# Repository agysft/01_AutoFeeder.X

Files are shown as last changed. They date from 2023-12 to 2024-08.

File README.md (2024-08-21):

# AutoFeeder
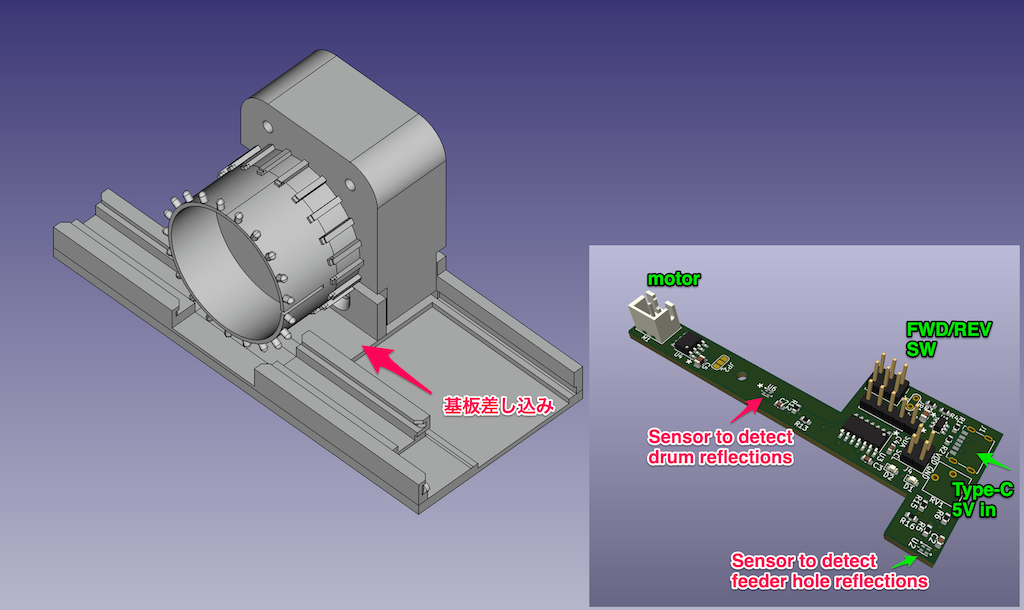
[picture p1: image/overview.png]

This is a test project for an auto-feeder for CompactPnP. When the switch is pressed, the feeder moves one frame. It includes a program and a schematic. The program was written in PIC MPLAB X IDE. The schematic is written in KiCAD and the printed circuit board is made. The structure was made with a 3D printer.

---
これはCompactPnP用のオートフィーダーのテスト用プロジェクトです。スイッチが押されるとフィーダーが一コマ移動します。プログラムと回路図を含みます。プログラムはPIC MPLAB X IDEで書きました。回路図はKiCADで書き、プリント基板を作っています。構造物は3Dプリンターで作りました。

---
### Rev.01
* [demo](image/ezgif.com-video-to-gif-converted.gif)
* [schematics](schematics/AutoFeeder_Drum-type_new/20231123_R1/AutoFeeder_Drum-type.pdf) 
* block chart
```mermaid
graph LR
  A[Timer2]-->B[PWM3]-->C
  subgraph BA6211
  C[FWD]
  E[REV]
  end
  A-->D[PWM4]-->E
  F[Sensor0]-->|-|M[CMP2]-->N[LED Green]
    L[FVR 1.024V]-->|+|M
    L-->|+|Q
  I[Sensor1]-->|-|Q[CMP1]-->K[LED Red]
```
---

### Rev.02
フォトセンサーの感度を切り替える回路と、ドラムの角度を取得するためのAS5600という磁気センサーと、I2CのLCDを接続できるようにしました。Add a circuit to switch the sensitivity of the photo sensor, a magnetic sensor named AS5600 to get the angle of the drum, and the LCD.
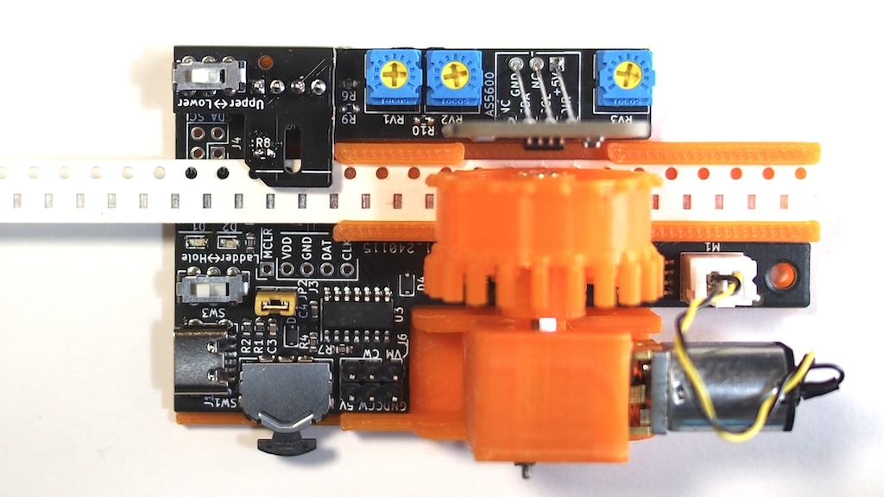
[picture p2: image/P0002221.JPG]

* [demo](image/20240212_AutoFeederTest-ezgif.com-video-to-gif-converter.gif)
* [schematics](schematics/AutoFeeder_Drum-type_new/20240107_Rev02/AutoFeeder_Drum-type.pdf) 
* block chart

```mermaid
graph LR
  G[Senror1 Radder detector]--> S
  F[Sensor0 Tape-hole detector]--> S
  S{Switch} -->| M- |M
  subgraph BA6211
  C[FWD]
  E[REV]
  end
  BA6211 --- Z[Motor]
  subgraph PIC16F1705
  A[Timer2 50KHz]-->D
  A-->B
  B[PWM3 -- RC5]---C
  D[PWM4 -- RC4]---E
  L[FVR 2.048V]-->| P+ |M[CMP2 -- RA0]
  RA4[GPIO RA4 Open Drain]
  RA5[GPIO RA5 Open Drain]
  end
  M-->N[LED]
  AS5600---|I2C|PIC16F1705
  PIC16F1705---|I2C|LCD
  
  H[Optical Sensor Sensitivity Selector]---RA4
  H---RA5
```

* High-Endurance Flash memory (HEF) usage 0x1F80-0x1F9F
  | Offset Address | note (1 word = 14-bit wide) |
  |:--:|---- 
  | 25 .. 31 | No Use |
  | 2 .. 24 | Tape hole position data (12-bit wide) |
  | 1 | Tape-Color data (White/Transparent/Black)|
  | 0 | AS5600 Magnetic data of origin (12-bit wide) |
* HEF 0x1FA0-0x1FFF is not use.

---
### AutoFeeder2 Rev.1
Autofeeder Rev.02の機能はそのままに、基板を縦置きする事で省スペース化を図りました。また、透過型のフォトインタラプターCNZ1023を使えるようにしました。The functions of the Autofeeder are retained, but the board is placed vertically to save space. Transmissive photo interrupter CNZ1023 can also be used.
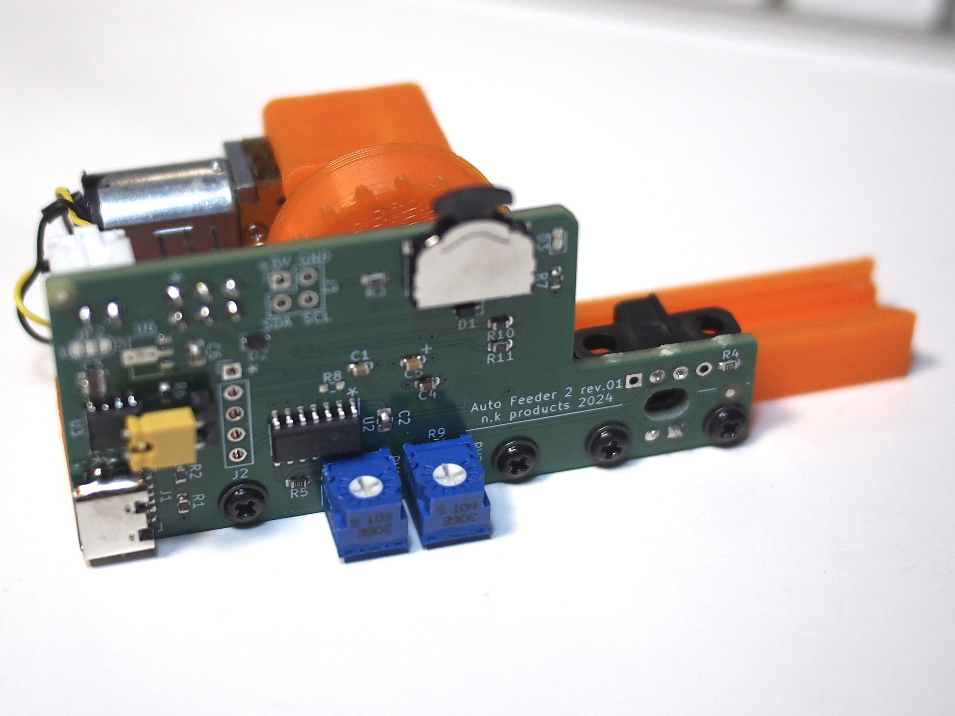
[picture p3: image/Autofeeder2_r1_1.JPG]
AF2R1_pict1


* [demo](image/20240803_AutoFeeder_Test2.gif)
* [schematics](schematics/AutoFeeder_Drum-type_2/20240519_AF2_rev1/AutoFeeder_Drum-type.pdf) 

---
### Tips

* PIC16F1705でI2C を設定する。何故か400kHzに設定するとハングします。「Registers」で SSP1ADD = 0x9 (=400KHz)に設定することは可能。
  
  Setting I2C on the PIC16F1705. It hangs when set to 400kHz. It is possible to set SSP1ADD = 0x9 (=400KHz) in "Registers".
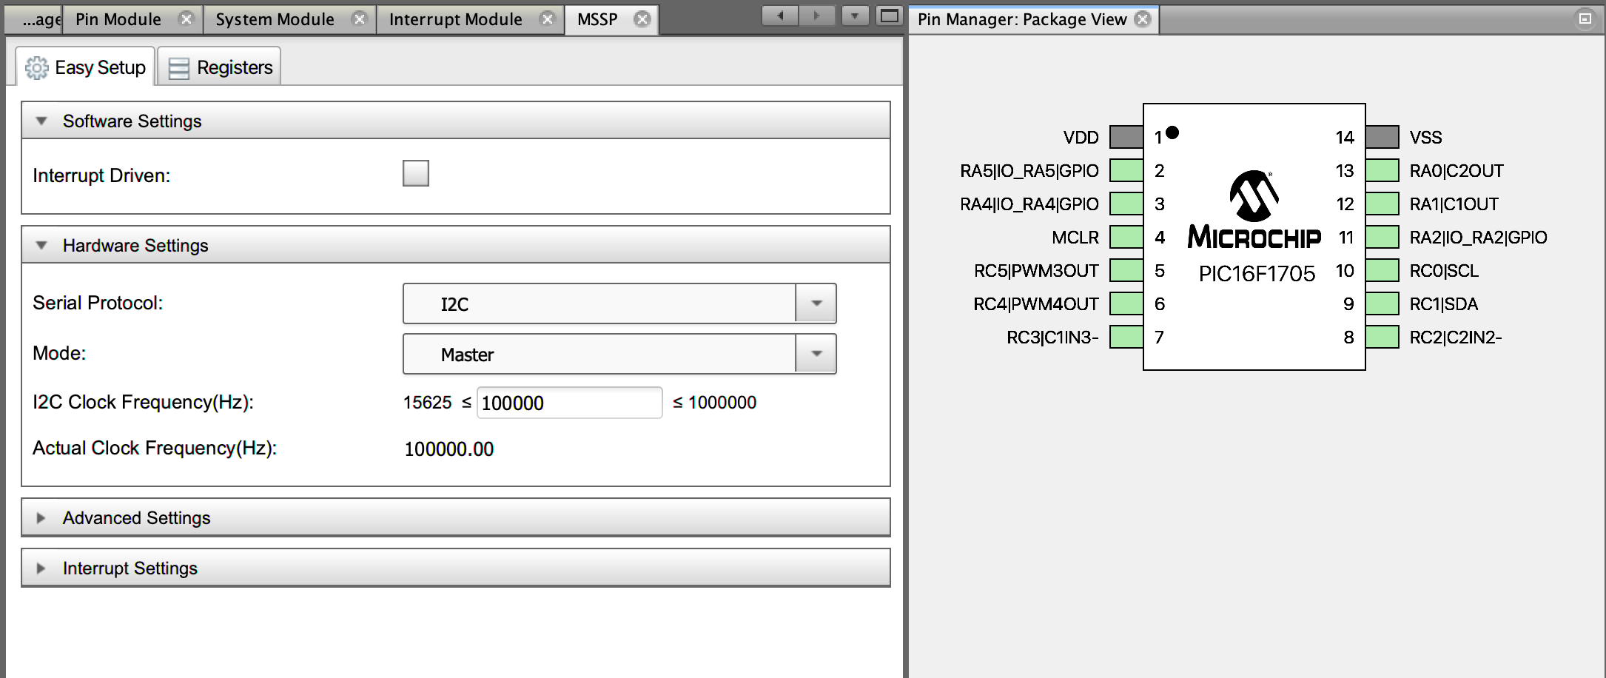
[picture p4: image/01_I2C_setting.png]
  

* このI2Cのサンプルコードがよく出来ていてそのままincludeして使える。
  This I2C sample code is well done and can be included and used as is.
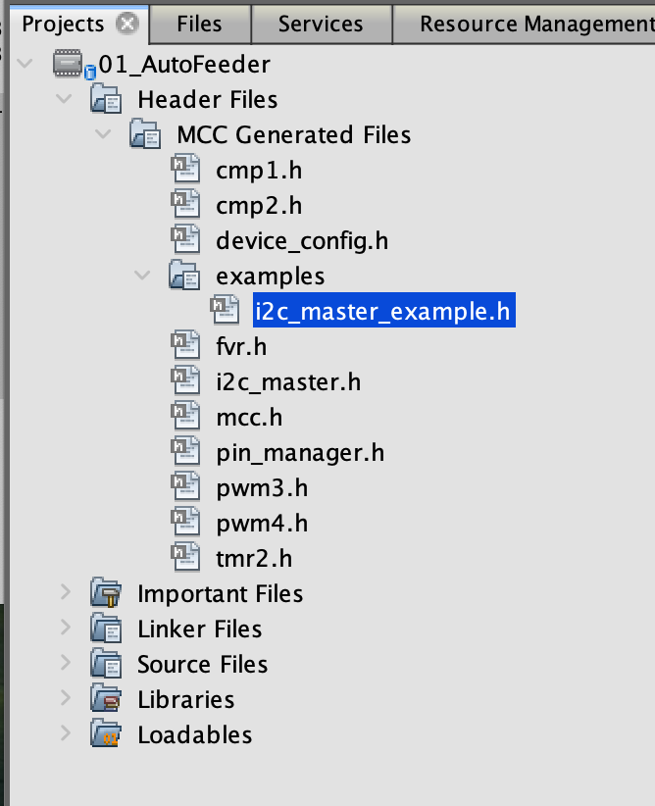
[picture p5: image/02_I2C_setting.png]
  

* HEF-block範囲にプログラムが書かれないようにする設定。
  Settings to prevent programs from being written in the HEF-block range
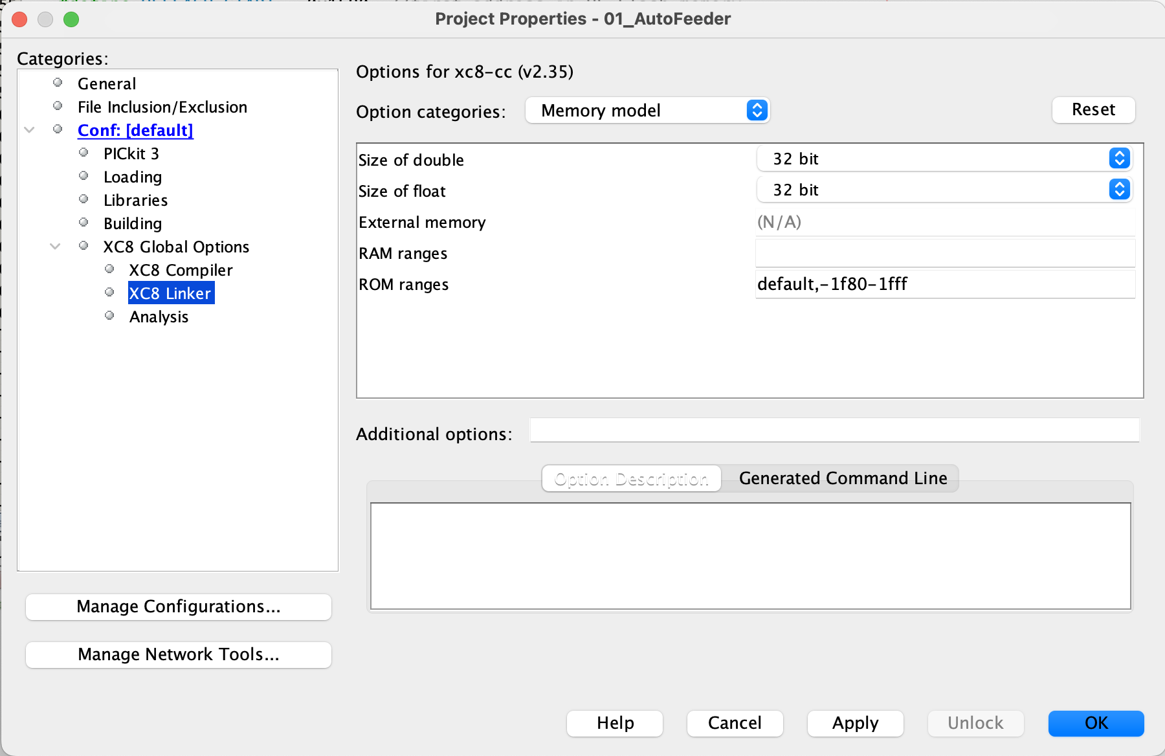
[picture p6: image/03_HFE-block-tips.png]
  

* PICに書いた時にHEFブロックが初期化されない設定。
  Settings to prevent the HEF-block from being initialized when writing to the PIC
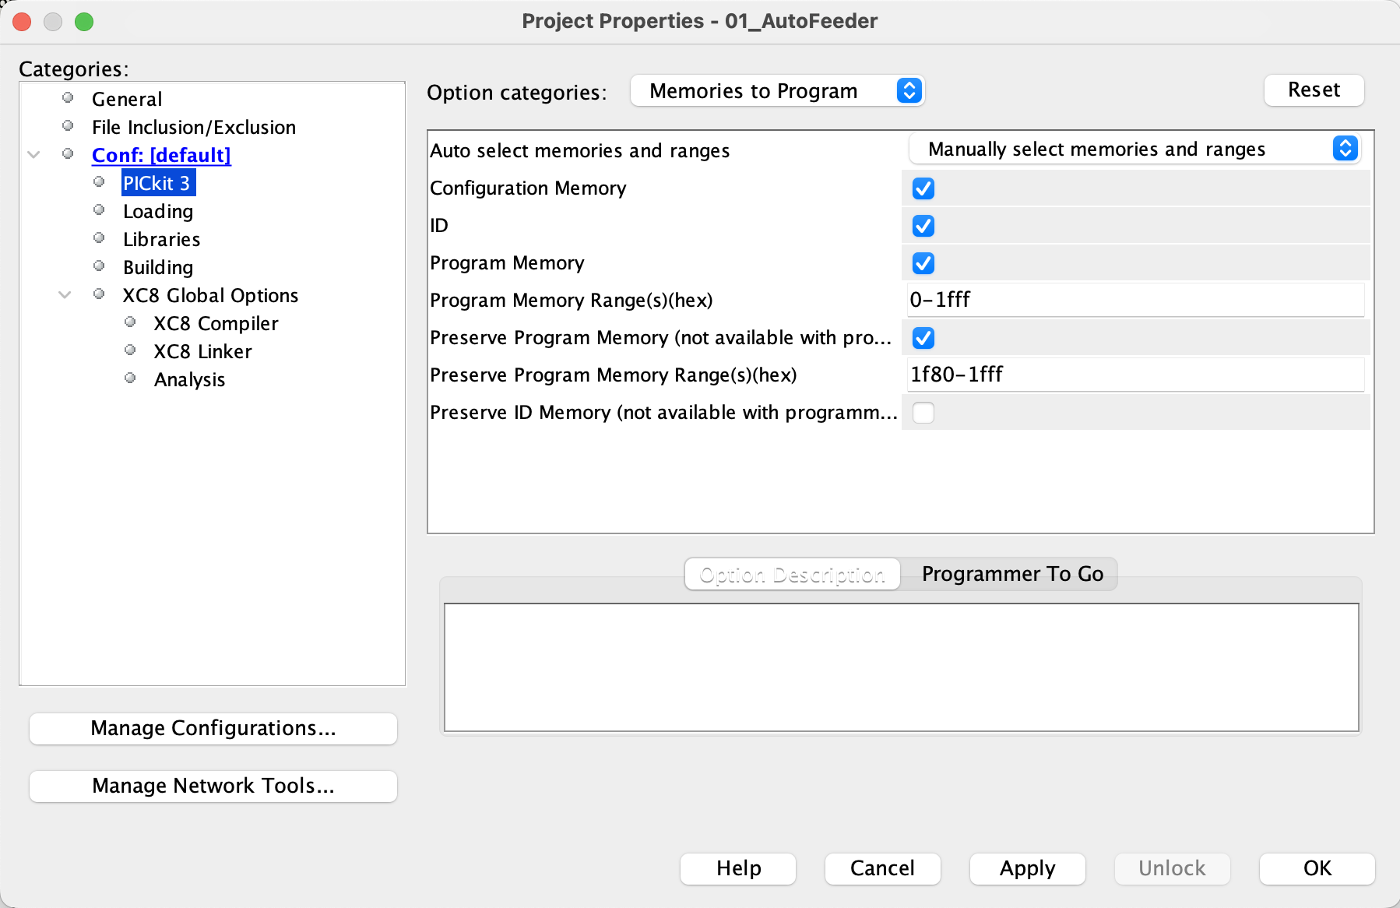
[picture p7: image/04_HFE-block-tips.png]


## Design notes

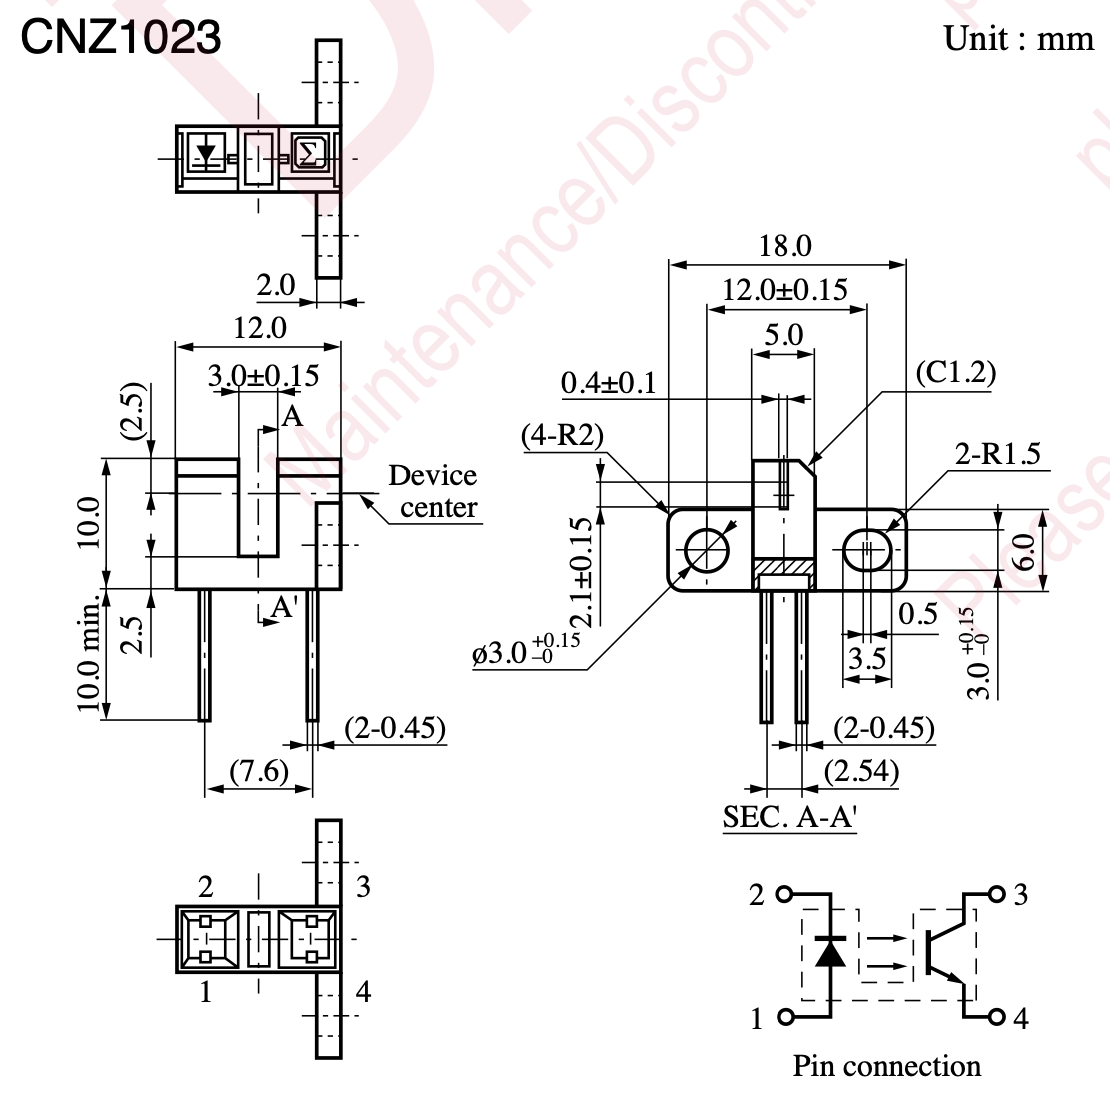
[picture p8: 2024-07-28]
schematics/AutoFeeder_Drum-type_2/CNZ1023.png

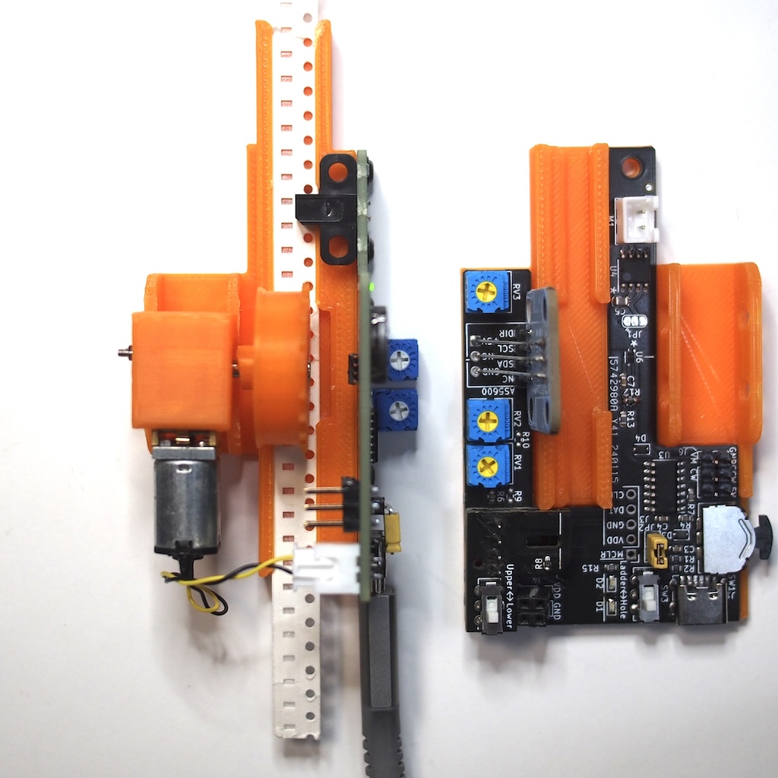
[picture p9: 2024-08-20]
image/Autofeeder2_r1_2.JPG

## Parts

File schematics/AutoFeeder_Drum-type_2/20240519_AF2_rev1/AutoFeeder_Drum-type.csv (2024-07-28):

ID | 指定子 | パッケージ | 数量 | 名称 | 供給業者、参考資料
1 | R7,R3,R4 | R_0603_1608Metric | 3 | 1k
2 | U3 | SOIC-8_3.9x4.9mm_P1.27mm | 1 | ZXBM5210-S
3 | R5 | R_0603_1608Metric | 1 | 1.5k
4 | J3 | PinHeader_2x02_P2.54mm_Vertical | 1 | Conn_02x02_Odd_Even
5 | C1 | C_0603_1608Metric | 1 | 0.01u
6 | C5 | C_0603_1608Metric | 1 | 1u
7 | JP2 | SolderJumper-3_P1.3mm_Bridged12_RoundedPad1.0x1.5mm_NumberLabels | 1 | SolderJumper_3_Bridged12
8 | J2 | PinHeader_1x05_P2.54mm_Vertical | 1 | Conn_01x05
9 | U2 | SOIC-14_3.9x8.7mm_P1.27mm | 1 | PIC16F1705-I/SO
10 | C2,C6 | C_0805_2012Metric | 2 | 0.1u
11 | R11,R2,R1,R10 | R_0603_1608Metric | 4 | 5.1k
12 | R6 | R_0603_1608Metric | 1 | 10k
13 | U6 | SOT-89-3 | 1 | L78L05_SOT89
14 | RV2,RV1 | Potentiometer_ACP_CA6-H2,5_Horizontal | 2 | 20k
15 | D3 | LED_0603_1608Metric | 1 | LED
16 | J1 | USB_C_6 | 1 | USB_C_Receptacle_6
17 | SW1 | THMU26_2 | 1 | TMHU26
18 | R9 | R_0603_1608Metric | 1 | 20k
19 | R8 | R_0603_1608Metric | 1 | 9.1k
20 | D2,D1 | D_SOD-323F | 2 | 1SS355VM
21 | C4 | C_0603_1608Metric | 1 | 0.1u
22 | J7 | PinHeader_1x04_P2.54mm_Vertical | 1 | Conn_01x04
23 | U5 | NJL5901AR-1 | 1 | NJL5901AR-1
24 | C3 | C_0805_2012Metric | 1 | 10u
25 | JP3 | SolderJumper-3_P1.3mm_Bridged12_RoundedPad1.0x1.5mm | 1 | SolderJumper_3_Bridged12
26 | M1 | JST_XH_B2B-XH-A_1x02_P2.50mm_Vertical | 1 | Motor_DC
27 | JP1 | PinHeader_1x02_P2.54mm_Horizontal | 1 | Jumper_2_Bridged
28 | J6,J5 | PinHeader_1x01_P2.54mm_Vertical | 2 | Conn_01x01
29 | U4 | SOP-8_3.9x4.9mm_P1.27mm | 1 | AS5600
30 | U1 | CNZ1023 | 1 | CNZ1023
31 | J4 | PinHeader_2x03_P2.54mm_Vertical | 1 | Conn_02x03_Odd_Even

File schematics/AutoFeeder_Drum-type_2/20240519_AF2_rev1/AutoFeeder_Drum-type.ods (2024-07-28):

ID | 指定子 | パッケージ | 数量 | 名称 | 供給業者、参考資料 |  | 販売コード |  |  | 購入数 | 価格合計
5 | C1 | C_0603_1608Metric | 1 | 0.01u |  |  |  |  |  |  | 0
10 | C2,C6 | C_0805_2012Metric | 2 | 0.1u |  |  |  |  |  |  | 0
24 | C3 | C_0805_2012Metric | 1 | 10u |  |  |  |  |  |  | 0
21 | C4 | C_0603_1608Metric | 1 | 0.1u |  |  | 116143 | 110 |  | 1 | 110 | x40個入り
6 | C5 | C_0603_1608Metric | 1 | 1u |  |  | 114526 | 100 |  | 1 | 100 | x20個入り
20 | D2,D1 | D_SOD-323F | 2 | 1SS355VM |  |  |  |  |  |  | 0
15 | D3 | LED_0603_1608Metric | 1 | LED 黄色 |  | * | 111880 | 100 | 100 | 1 | 100 | x10個入り
 |  |  | 1 | LED 白色 |  |  | 111882 | 200 | 200 | 2 | 400 | x20個入り
16 | J1 | USB_C_6 | 1 | USB_C_Receptacle_6 |  |  |  |  |  |  | 0
8 | J2 | PinHeader_1x05_P2.54mm_Vertical | 1 | Conn_01x05 |  |  |  |  |  |  | 0
4 | J3 | PinHeader_2x02_P2.54mm_Vertical | 1 | Conn_02x02_Odd_Even |  |  |  |  |  |  | 0
31 | J4 | PinHeader_2x03_P2.54mm_Vertical | 1 | Conn_02x03_Odd_Even |  |  |  |  |  |  | 0
28 | J6,J5 | PinHeader_1x01_P2.54mm_Vertical | 2 | Conn_01x01 |  |  |  |  |  |  | 0
22 | J7 | PinHeader_1x04_P2.54mm_Vertical | 1 | Conn_01x04 |  |  |  |  |  |  | 0
27 | JP1 | PinHeader_1x02_P2.54mm_Horizontal | 1 | Jumper_2_Bridged |  |  |  |  |  |  | 0
7 | JP2 | SolderJumper-3_P1.3mm_Bridged12_RoundedPad1.0x1.5mm_NumberLabels | 1 | SolderJumper_3_Bridged12 |  |  |  |  |  |  | 0
25 | JP3 | SolderJumper-3_P1.3mm_Bridged12_RoundedPad1.0x1.5mm | 1 | SolderJumper_3_Bridged12 |  |  |  |  |  |  | 0
26 | M1 | JST_XH_B2B-XH-A_1x02_P2.50mm_Vertical | 1 | Motor_DC |  |  |  |  |  |  | 0
11 | R11,R2,R1,R10 | R_0603_1608Metric | 4 | 5.1k |  |  |  |  |  |  | 0
3 | R5 | R_0603_1608Metric | 1 | 1.5k |  |  |  |  |  |  | 0
12 | R6 | R_0603_1608Metric | 1 | 10k |  |  |  |  |  |  | 0
1 | R7,R3,R4 | R_0603_1608Metric | 3 | 1k |  |  |  |  |  |  | 0
19 | R8 | R_0603_1608Metric | 1 | 9.1k |  |  |  |  |  |  | 0
18 | R9 | R_0603_1608Metric | 1 | 20k |  |  |  |  |  |  | 0
14 | RV2,RV1 | Potentiometer_ACP_CA6-H2,5_Horizontal | 2 | 20k →100k |  | * | 113740 | 40 | 80 | 4 | 160
 |  |  | 2 | 10k |  |  | 113739 | 40 | 80 | 4 | 160
 |  |  | 2 | 半固定ボリューム GF063P 50kΩ |  |  | 114908 | 30 | 60 | 4 | 120
17 | SW1 | THMU26_2 | 1 | TMHU26 |  |  |  |  |  |  | 0
30 | U1 | CNZ1023 | 1 | CNZ1023 |  | * | 109668 | 20 | 20 | 4 | 80
9 | U2 | SOIC-14_3.9x8.7mm_P1.27mm | 1 | PIC16F1705-I/SO |  |  | 113571 | 170 | 170 | 4 | 680
2 | U3 | SOIC-8_3.9x4.9mm_P1.27mm | 1 | ZXBM5210-S BD6231(36V耐圧) |  |  | 105088 | 200 | 200 | 2 | 400
29 | U4 | SOP-8_3.9x4.9mm_P1.27mm | 1 | AS5600 |  |  |  |  |  |  | 0
23 | U5 | NJL5901AR-1 | 1 | NJL5901AR-1 |  |  |  |  |  |  | 0
13 | U6 | SOT-89-3 | 1 | L78L05_SOT89 NJM78L05SU3 |  | * | 111320 | 30 | 30 | 4 | 120
 |  |  | 1 | BatteryHolder_Keystone_2466_1xAAA |  |  | 102670 | 40 | 40 | 4 | 160
 |  |  | 1 | トロイダルコア FT-37-75 |  |  | 116922 | 150 | 150 | 4 | 600
 |  |  | 1 | 2種ポリウレタン銅線 2UEW 0.4mm 10m |  |  | 113709 | 220 | 220 | 1 | 220
 |  |  |  |  |  |  |  |  |  |  | 0
 |  |  |  |  |  |  |  |  |  |  | 0
 |  |  |  |  |  |  |  |  |  |  | 0
 |  |  |  |  |  |  |  |  |  |  | 0
 |  |  |  |  |  |  |  |  | 1350 |  | 3410

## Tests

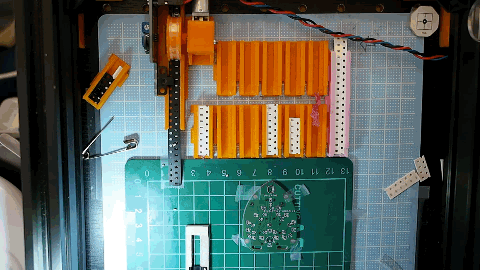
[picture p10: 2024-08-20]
image/20240803_AutoFeeder_Test2.gif

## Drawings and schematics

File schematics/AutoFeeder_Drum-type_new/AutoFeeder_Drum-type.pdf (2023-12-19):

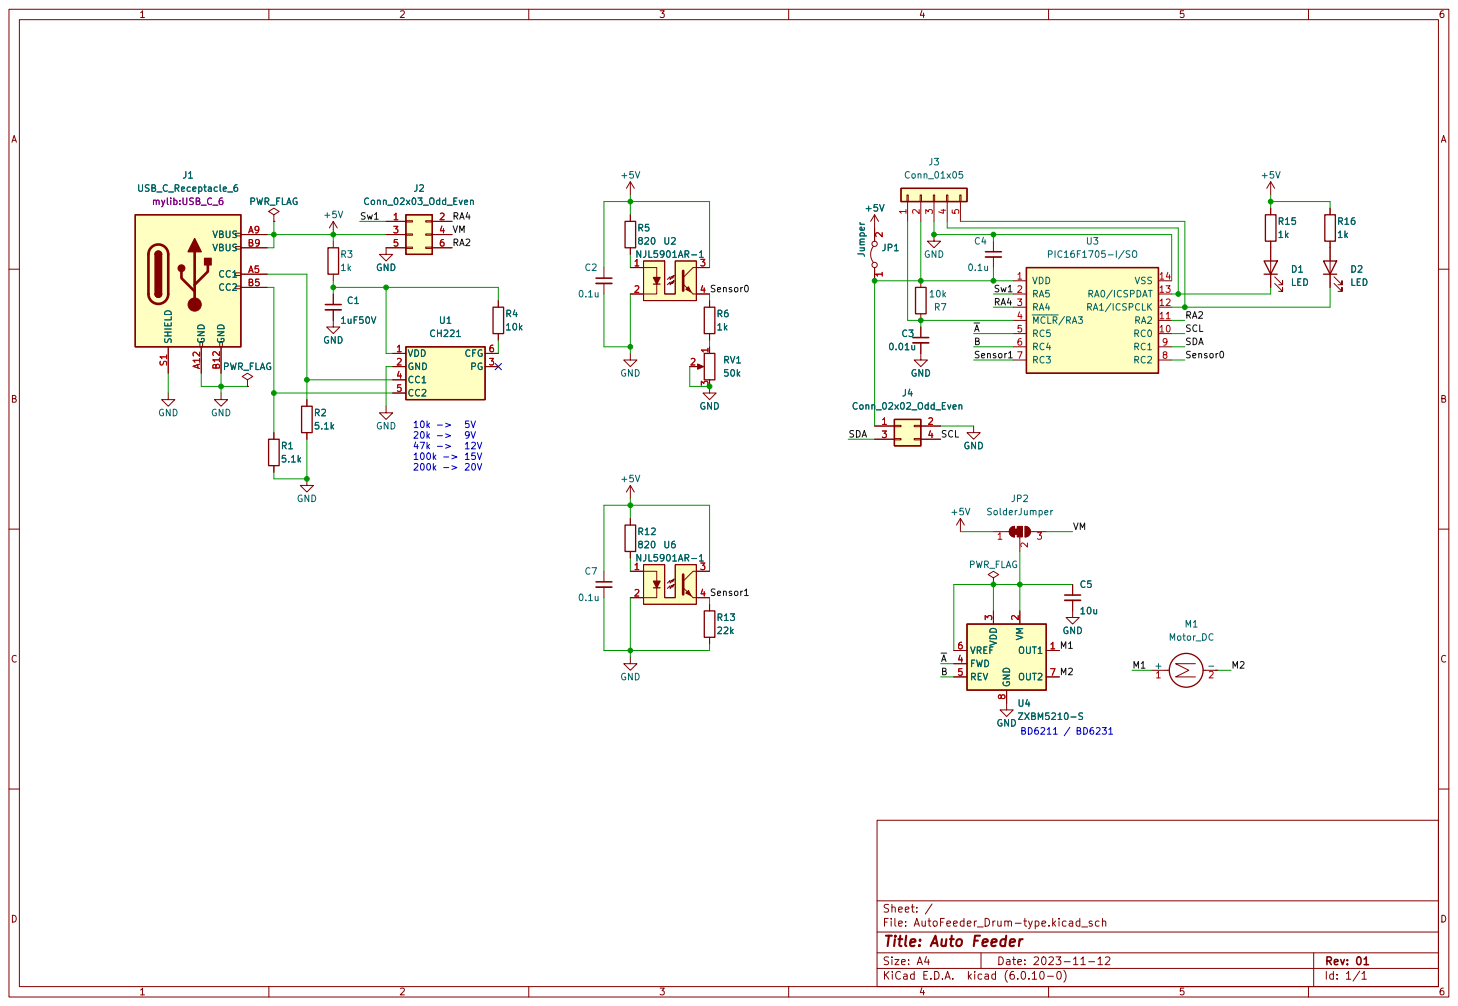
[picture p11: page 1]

1 2 JP1 Jumper GND GND OUT1 1 VM

3 FWD 4 REV 5 VREF 6 OUT2 7 GND

File: AutoFeeder_Drum-type.kicad_sch Sheet: /
Id: 1/1 Title: Auto Feeder

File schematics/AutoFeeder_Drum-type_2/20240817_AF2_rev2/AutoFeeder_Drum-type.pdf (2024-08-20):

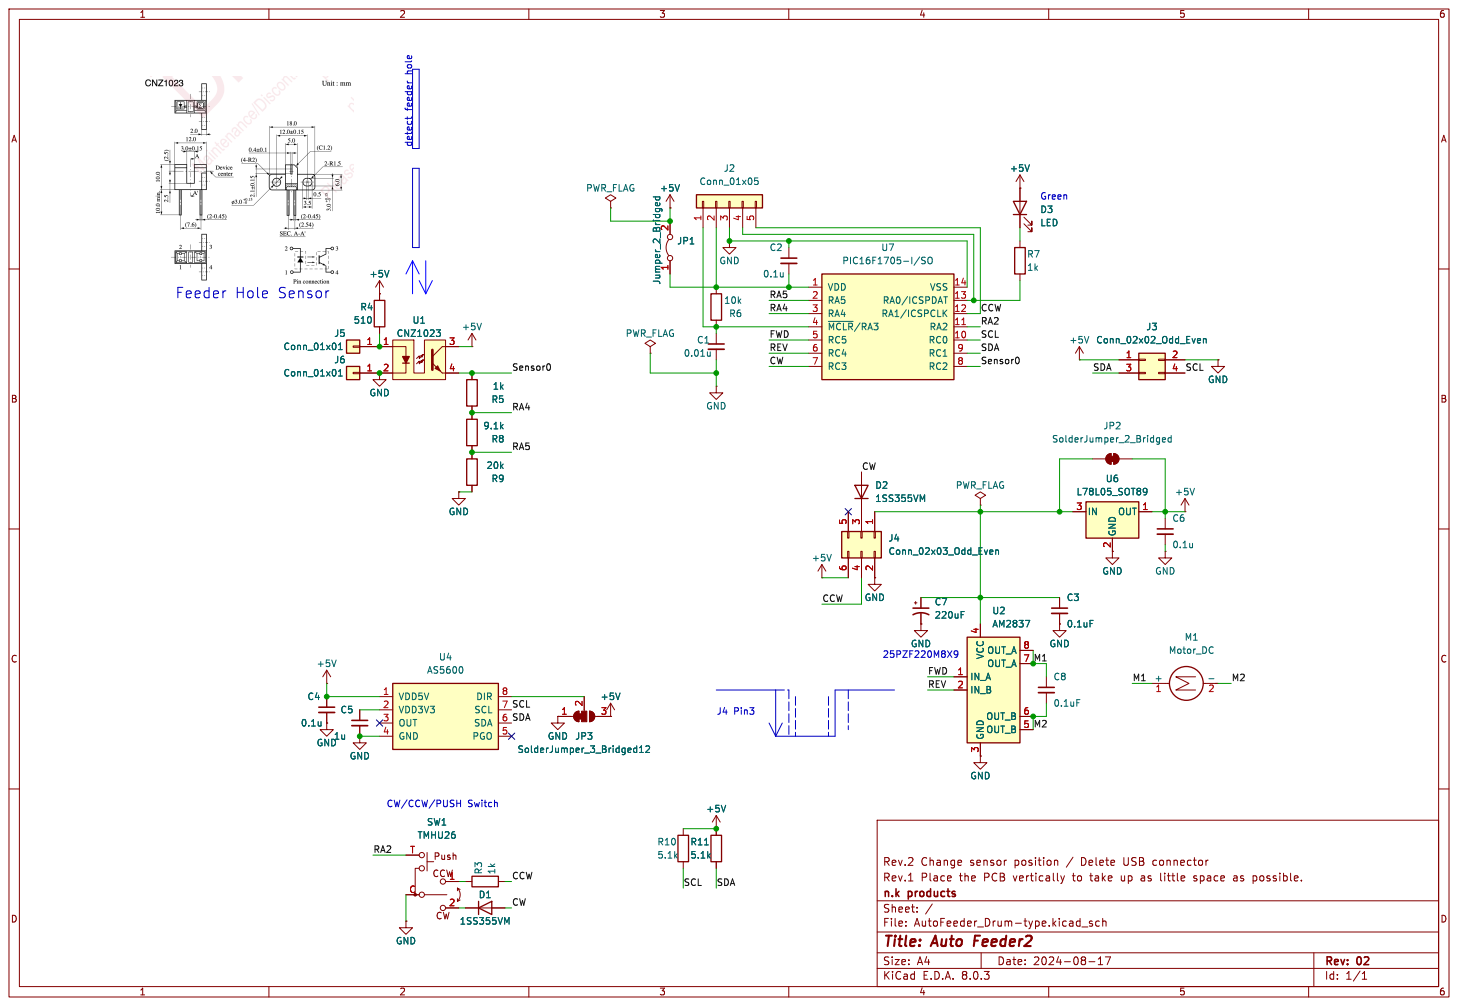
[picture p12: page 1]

Green detect feeder hole

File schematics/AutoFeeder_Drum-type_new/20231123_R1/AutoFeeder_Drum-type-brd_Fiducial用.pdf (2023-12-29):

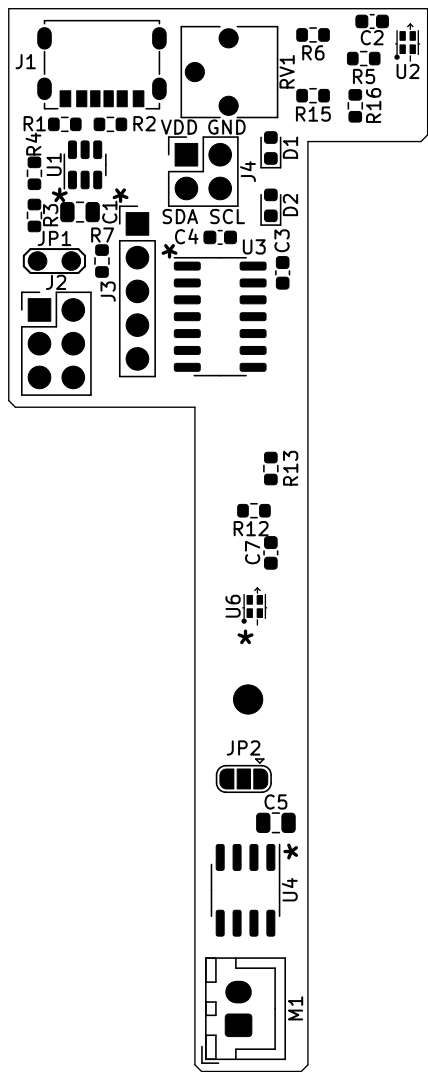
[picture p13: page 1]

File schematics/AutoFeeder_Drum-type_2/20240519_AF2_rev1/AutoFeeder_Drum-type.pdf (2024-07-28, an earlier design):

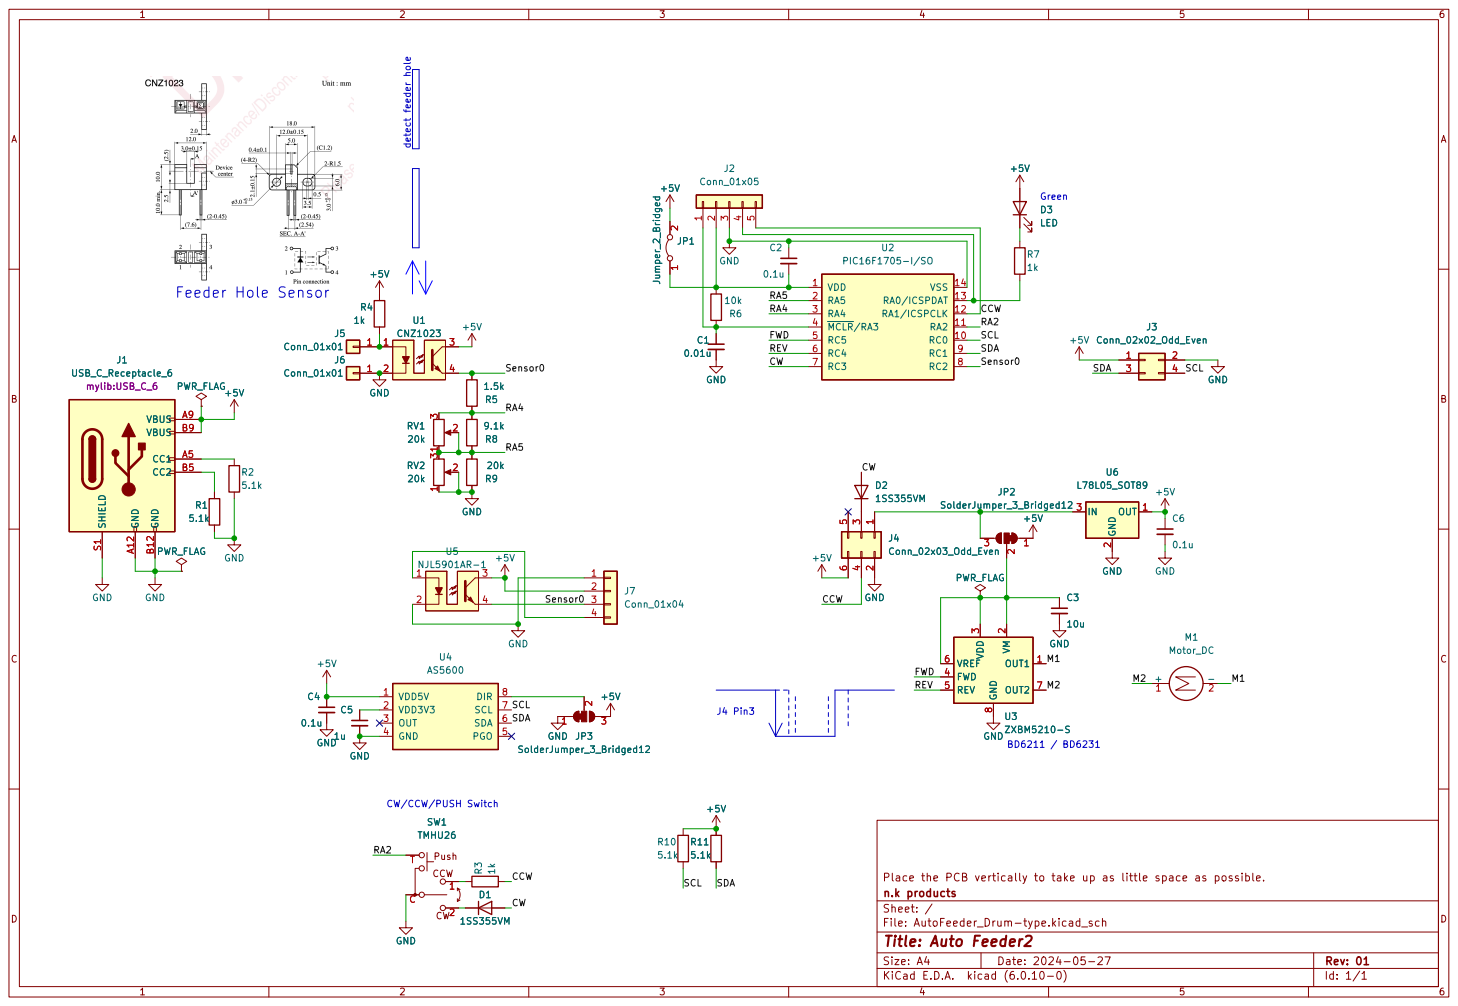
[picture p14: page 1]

J4 Pin3 CW/CCW/PUSH Switch Feeder Hole Sensor

3 FWD 4 REV 5 VREF 6 OUT2 7 GND

Place the PCB vertically to take up as little space as possible.
File: AutoFeeder_Drum-type.kicad_sch Sheet: / n.k products

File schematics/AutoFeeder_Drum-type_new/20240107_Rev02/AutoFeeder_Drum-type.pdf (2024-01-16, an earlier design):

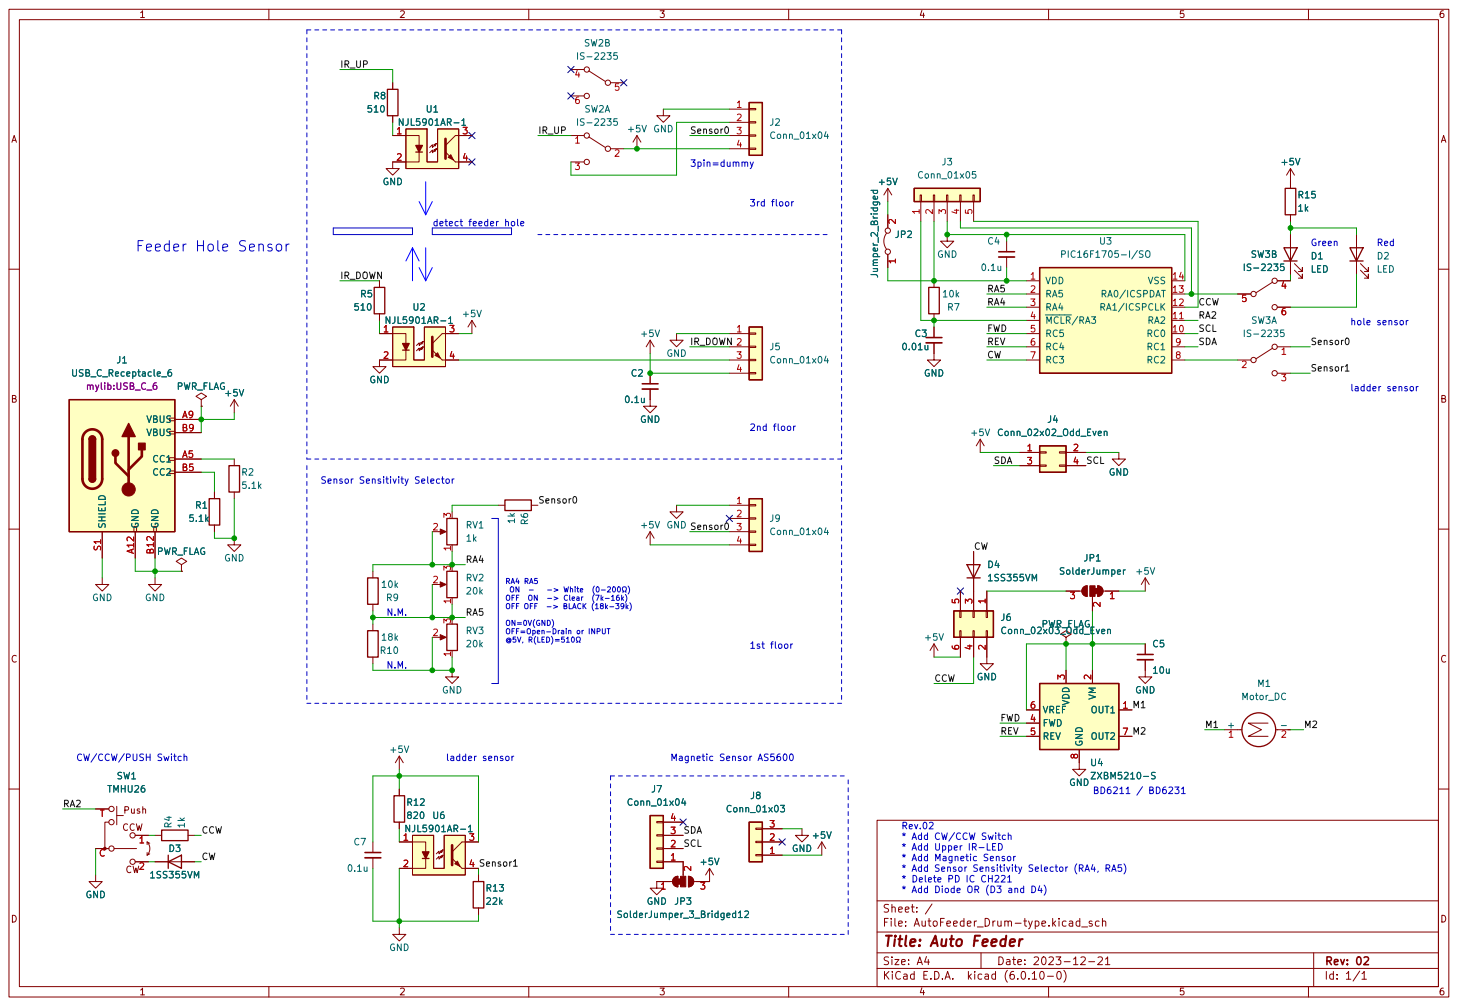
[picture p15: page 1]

þÿ ON  -   -> White  (0-200©) OFF ON -> Clear (7k-16k) OFF OFF -> BLACK (18k-39k) ON=0V(GND) OFF=Open-Drain or INPUT

* Add Diode OR (D3 and D4) 1st floor Magnetic Sensor AS5600

3 FWD 4 REV 5 VREF 6 OUT2 7 GND

* Add CW/CCW Switch
* Add Upper IR-LED
* Add Magnetic Sensor
* Add Sensor Sensitivity Selector (RA4, RA5) * Delete PD IC CH221

Id: 1/1 Title: Auto Feeder

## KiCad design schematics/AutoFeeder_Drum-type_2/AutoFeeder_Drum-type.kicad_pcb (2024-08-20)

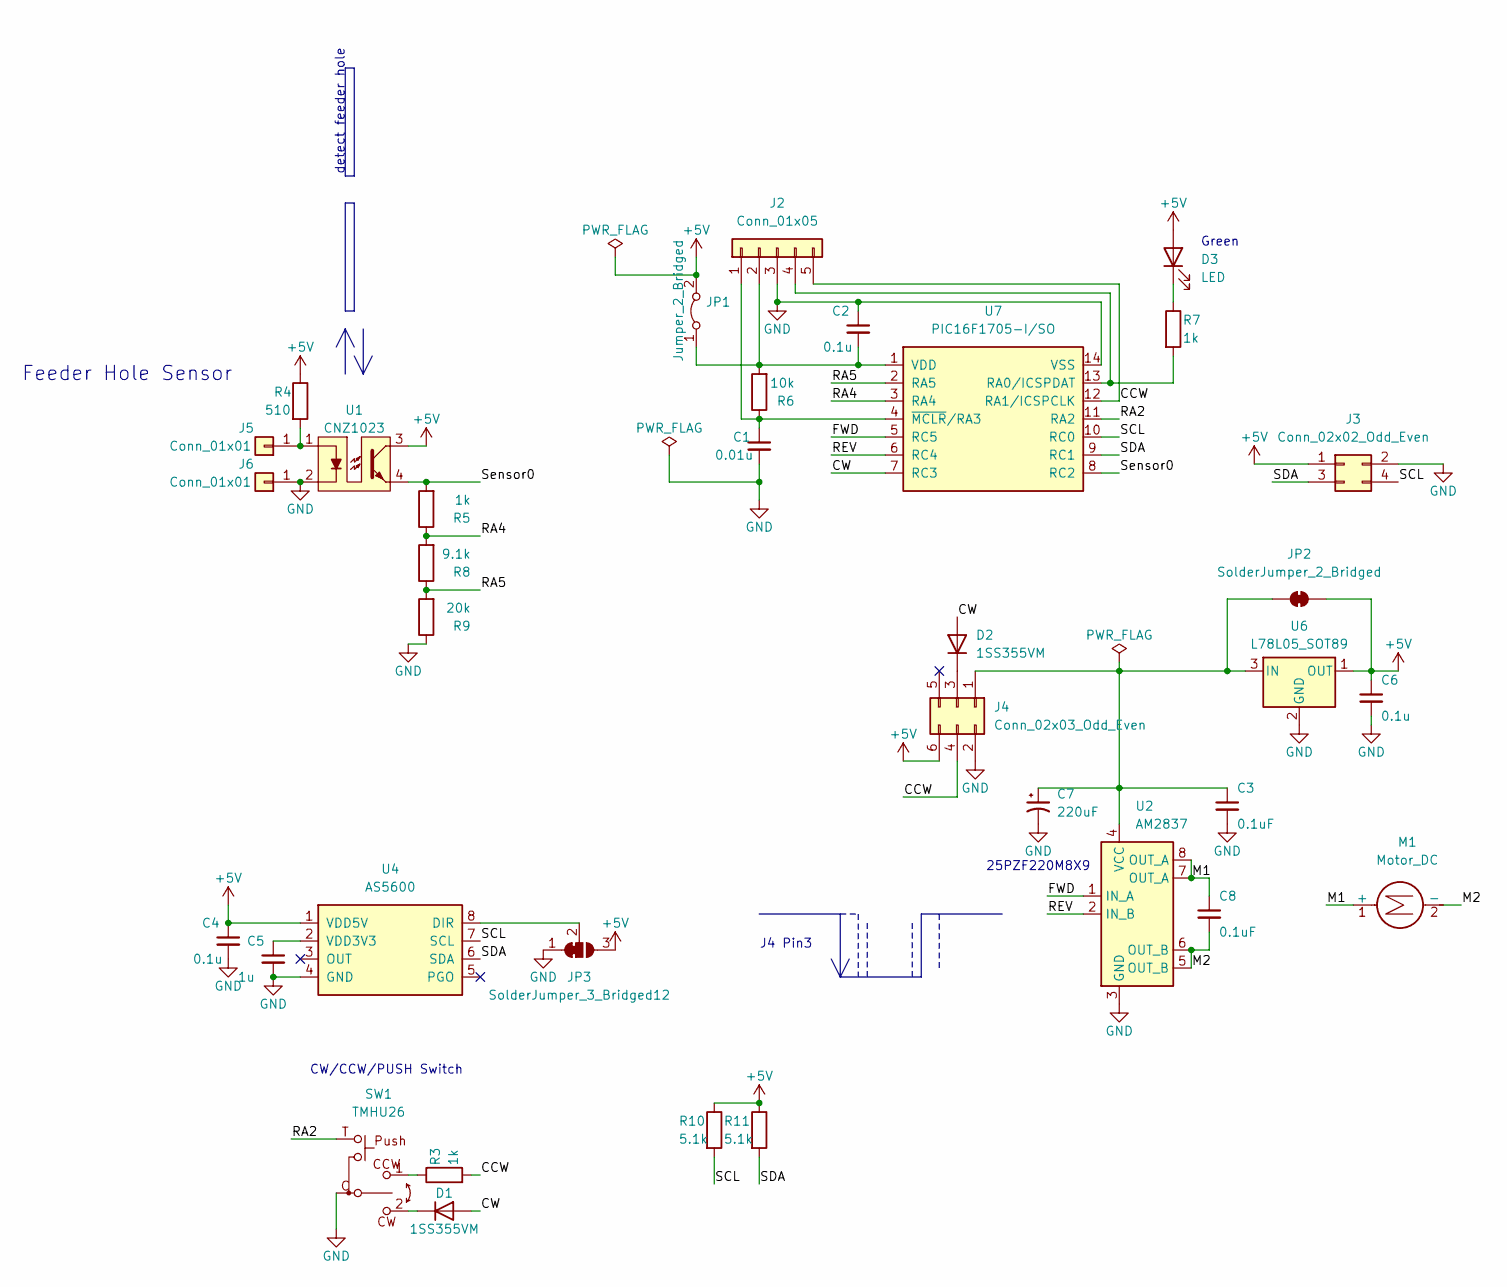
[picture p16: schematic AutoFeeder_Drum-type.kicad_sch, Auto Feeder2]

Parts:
C1: 0.01u; C_0603_1608Metric
C2, C4, C6: 0.1u; C_0805_2012Metric
C3, C8: 0.1uF; C_0805_2012Metric
C5: 1u; C_0805_2012Metric
C7: 220uF; CP_Radial_D8.0mm_P3.50mm
D1, D2: 1SS355VM; D_SOD-323F
D3: LED; LED_0603_1608Metric
J2: Conn_01x05; PinHeader_1x05_P2.54mm_Vertical
J3: Conn_02x02_Odd_Even; PinHeader_2x02_P2.54mm_Vertical
J4: Conn_02x03_Odd_Even; PinHeader_2x03_P2.54mm_Vertical
J5, J6: Conn_01x01; PinHeader_1x01_P2.54mm_Vertical
JP1: Jumper_2_Bridged; PinHeader_1x02_P2.54mm_Horizontal
JP2: SolderJumper_2_Bridged; SolderJumper-2_P1.3mm_Bridged_RoundedPad1.0x1.5mm
JP3: SolderJumper_3_Bridged12; SolderJumper-3_P1.3mm_Bridged12_RoundedPad1.0x1.5mm
M1: Motor_DC; JST_XH_B2B-XH-A_1x02_P2.50mm_Vertical
R3, R5, R7: 1k; R_0603_1608Metric
R4: 510; R_0603_1608Metric
R6: 10k; R_0603_1608Metric
R8: 9.1k; R_0603_1608Metric
R9: 20k; R_0603_1608Metric
R10, R11: 5.1k; R_0603_1608Metric
SW1: TMHU26; THMU26_2
U1: CNZ1023
U2: AM2837; SOIC-8_3.9x4.9mm_P1.27mm
U4: AS5600; SOP-8_3.9x4.9mm_P1.27mm
U6: L78L05_SOT89; SOT-89-3
U7: PIC16F1705-I/SO; SOIC-14_3.9x8.7mm_P1.27mm

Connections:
+5V: C4.1, C6.1, D3.2 (A), J3.1, J4.6, JP1.2 (B), JP2.2 (B), JP3.3 (B), R4.1, R10.1, R11.1, U1.3, U4.1 (VDD5V), U6.1 (OUT)
/CCW: J2.5, J4.4, R3.2, U7.12 (RA1/ICSPCLK)
/CW: D1.2 (A), D2.2 (A), U7.7 (RC3)
/FWD: U2.1 (IN_A), U7.5 (RC5)
/M1: C8.1, M1.1 (+), U2.7 (OUT_A), U2.8 (OUT_A)
/M2: C8.2, M1.2 (-), U2.5 (OUT_B), U2.6 (OUT_B)
/RA2: SW1.T, U7.11 (RA2)
/RA4: R5.1, R8.2, U7.3 (RA4)
/RA5: R8.1, R9.2, U7.2 (RA5)
/REV: U2.2 (IN_B), U7.6 (RC4)
/SCL: J3.4, R10.2, U4.7 (SCL), U7.10 (RC0)
/SDA: J3.3, R11.2, U4.6 (SDA), U7.9 (RC1)
/Sensor0: R5.2, U1.4, U7.8 (RC2)
GND: C1.2, C2.1, C3.2, C4.2, C5.2, C6.2, C7.2, J2.3, J3.2, J4.2, J6.1, JP3.1 (A), R9.1, SW1.C, U1.2, U2.3 (GND), U4.4 (GND), U6.2 (GND), U7.14 (VSS)
unnamed: D1.1 (K), SW1.2
unnamed: D2.1 (K), J4.3
unnamed: D3.1 (K), R7.1
unnamed: C1.1, J2.1, R6.1, U7.4 (~MCLR/RA3)
unnamed: C2.2, J2.2, JP1.1 (A), R6.2, U7.1 (VDD)
unnamed: J2.4, R7.2, U7.13 (RA0/ICSPDAT)
unnamed: C3.1, C7.1, J4.1, JP2.1 (A), U2.4 (VCC), U6.3 (IN)
unnamed: J5.1, R4.2, U1.1
unnamed: JP3.2 (C), U4.8 (DIR)
unnamed: R3.1, SW1.1
unnamed: C5.1, U4.2 (VDD3V3)

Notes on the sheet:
J4 Pin3
Green
detect feeder hole
CW/CCW/PUSH Switch
Feeder Hole Sensor
25PZF220M8X9

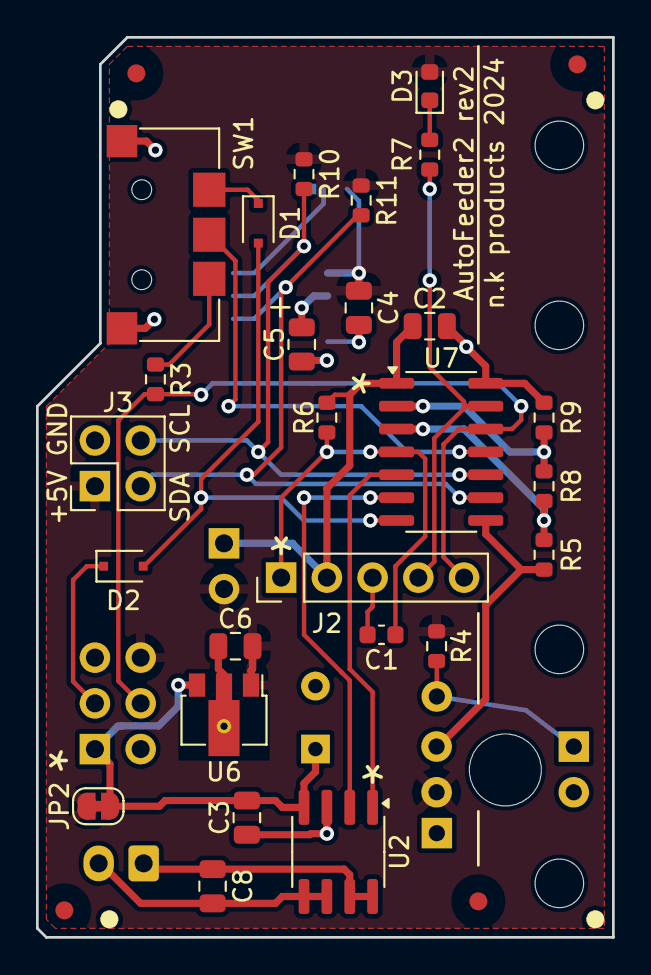
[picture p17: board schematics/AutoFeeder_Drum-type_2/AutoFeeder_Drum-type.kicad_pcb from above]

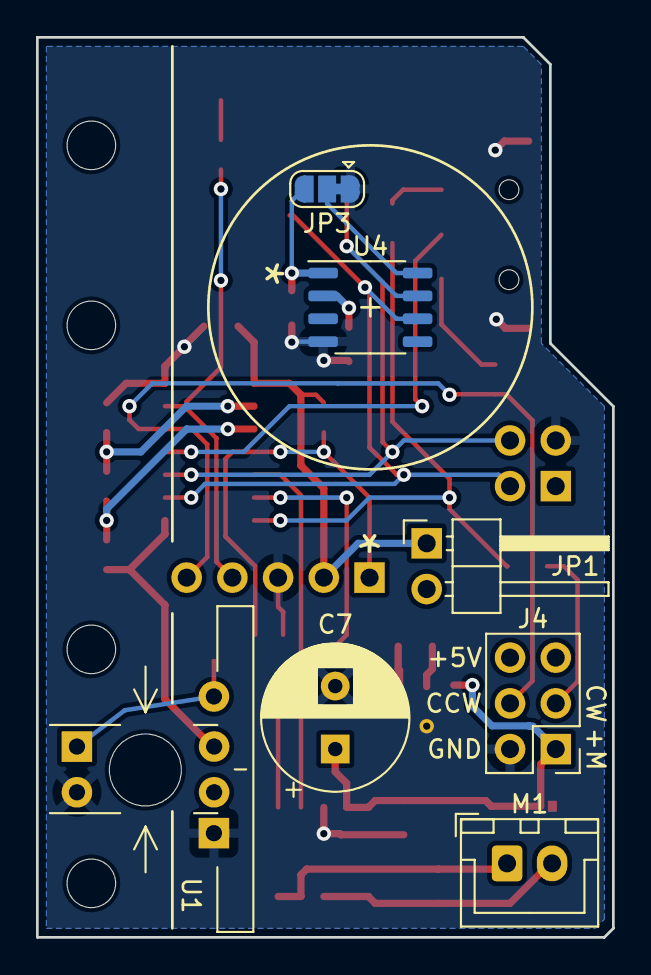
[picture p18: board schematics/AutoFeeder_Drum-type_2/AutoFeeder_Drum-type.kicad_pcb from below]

Board: 2 copper layers, 32.0 x 50.0 mm, 43 parts (9 on the bottom side), 25 nets.

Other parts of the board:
Fed1, Fed2, Fed3: Fiducial_1mm_Mask3mm
Fid4: Fiducial_1mm_Mask3mm
Fid5, Fid6, Fid7, Fid8: Fiducial_Silk

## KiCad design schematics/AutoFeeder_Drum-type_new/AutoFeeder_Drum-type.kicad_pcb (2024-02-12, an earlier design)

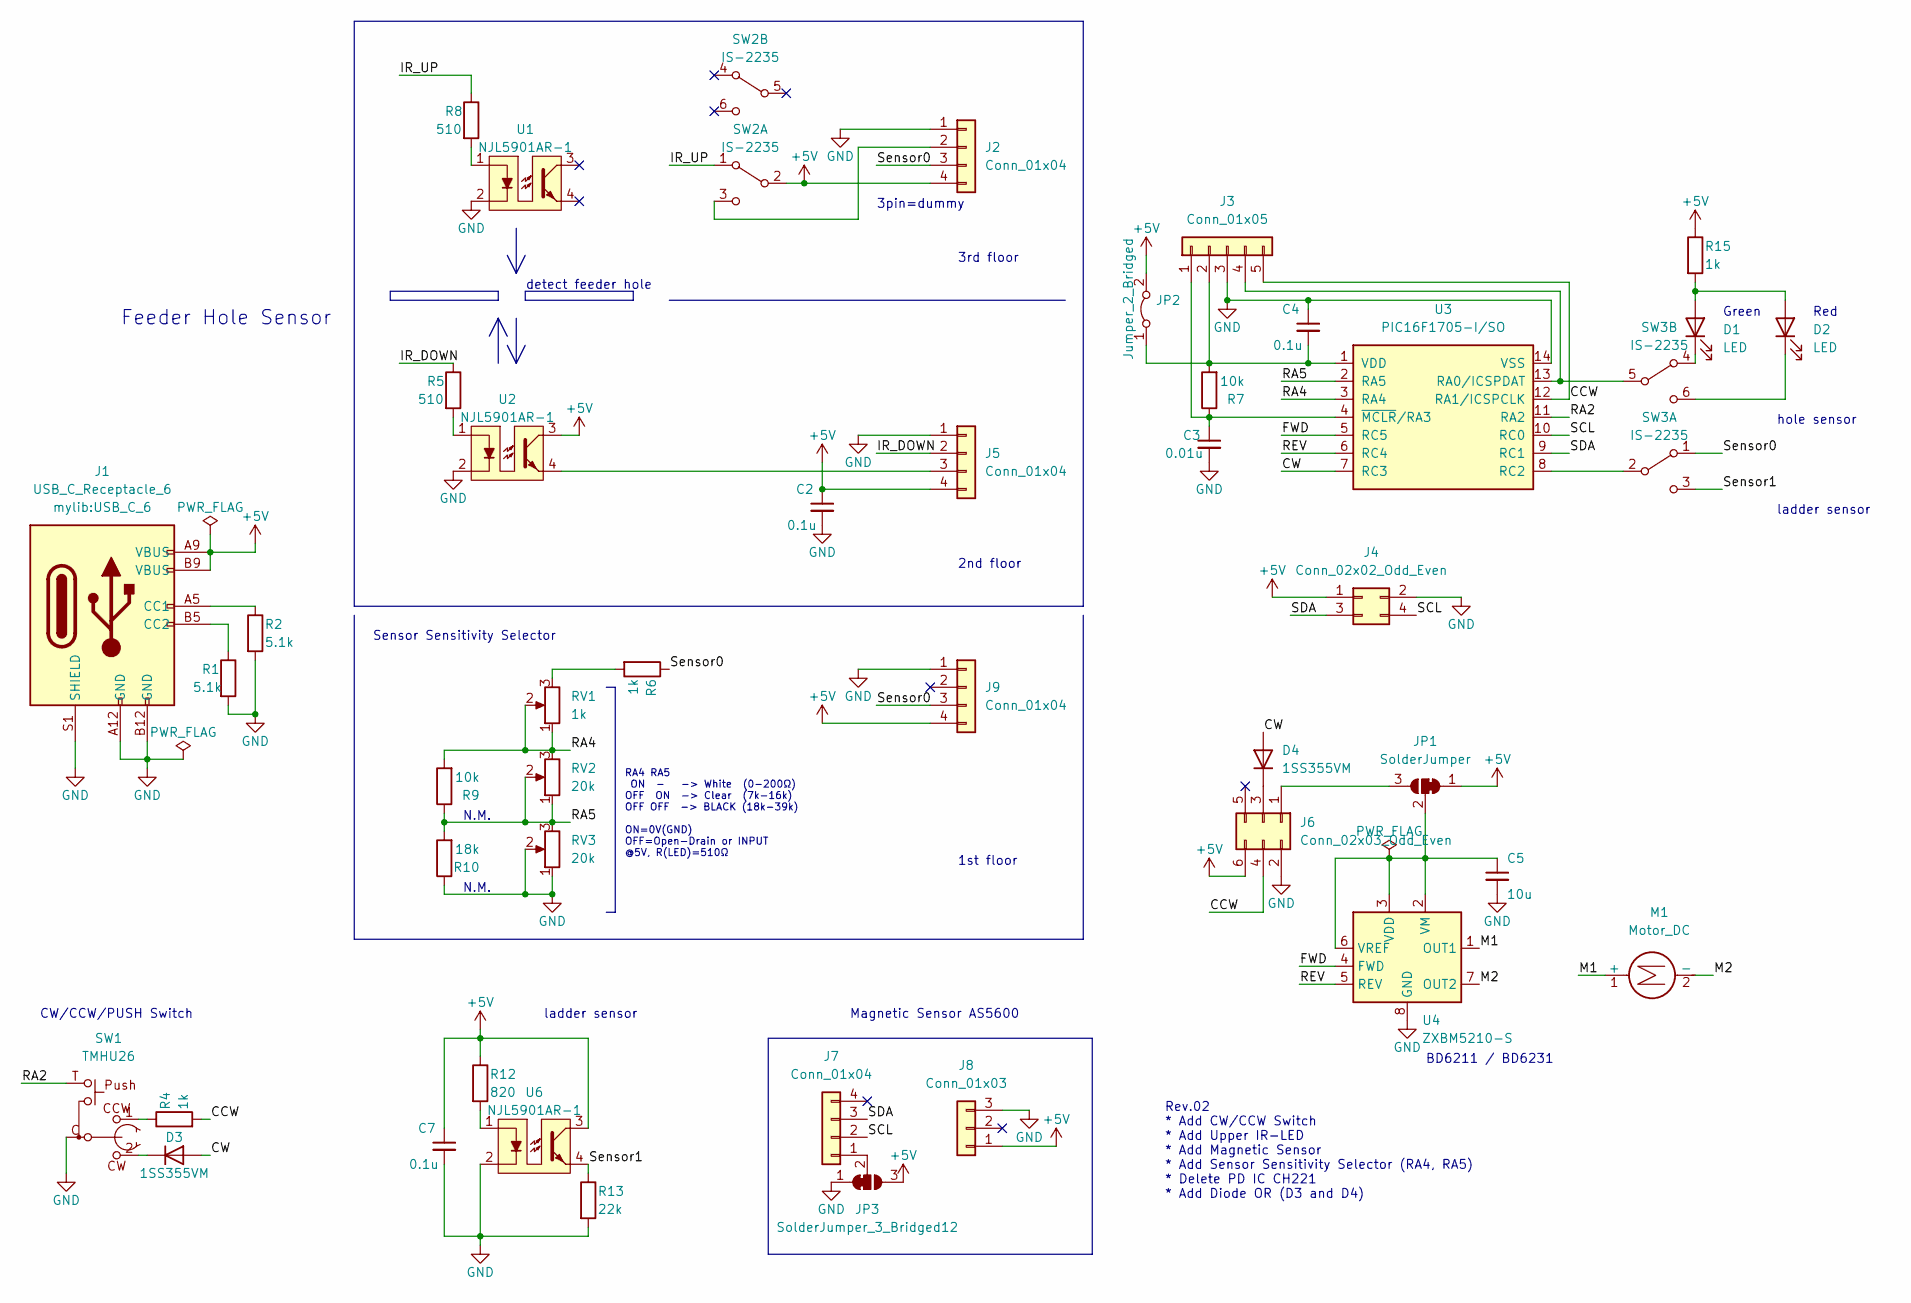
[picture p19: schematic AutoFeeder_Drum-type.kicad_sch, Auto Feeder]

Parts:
C2, C4, C7: 0.1u; C_0603_1608Metric
C3: 0.01u; C_0603_1608Metric
C5: 10u; C_0805_2012Metric
D1, D2: LED; LED_0603_1608Metric
D3, D4: 1SS355VM; D_SOD-323F
J1: USB_C_Receptacle_6; USB_C_6
J2, J5, J7, J9: Conn_01x04; PinHeader_1x04_P2.54mm_Vertical
J3: Conn_01x05; PinHeader_1x05_P2.54mm_Vertical
J4: Conn_02x02_Odd_Even; PinHeader_2x02_P2.54mm_Vertical
J6: Conn_02x03_Odd_Even; PinHeader_2x03_P2.54mm_Vertical
J8: Conn_01x03; PinHeader_1x03_P2.54mm_Vertical
JP1: SolderJumper; SolderJumper-3_P1.3mm_Bridged12_RoundedPad1.0x1.5mm
JP2: Jumper_2_Bridged; PinHeader_2x01_P2.54mm_Vertical
JP3: SolderJumper_3_Bridged12; SolderJumper-3_P1.3mm_Bridged12_RoundedPad1.0x1.5mm
M1: Motor_DC; JST_XH_B2B-XH-A_1x02_P2.50mm_Vertical
R1, R2: 5.1k; R_0603_1608Metric
R4, R6, R15: 1k; R_0603_1608Metric
R5, R8: 510; R_0603_1608Metric
R7, R9: 10k; R_0603_1608Metric
R10: 18k; R_0603_1608Metric
R12: 820; R_0603_1608Metric
R13: 22k; R_0603_1608Metric
RV1: 1k; Potentiometer_Vishay_T73YP_Vertical
RV2, RV3: 20k; Potentiometer_Vishay_T73YP_Vertical
SW1: TMHU26; THMU26_2
SW2, SW3: IS-2235; Slide-SW-IS-2235
U1, U2, U6: NJL5901AR-1
U3: PIC16F1705-I/SO; SOIC-14_3.9x8.7mm_P1.27mm
U4: ZXBM5210-S; SOIC-8_3.9x4.9mm_P1.27mm

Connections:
+5V: C2.1, C7.1, J1.A9 (VBUS), J1.B9 (VBUS), J2.4, J4.1, J5.4, J6.6, J8.1, J9.4, JP1.1 (A), JP2.2 (B), JP3.3 (B), R12.1, R15.1, SW2.2 (B), U2.3, U6.3
/CCW: J3.5, J6.4, R4.2, U3.12 (RA1/ICSPCLK)
/CW: D3.2 (A), D4.2 (A), U3.7 (RC3)
/FWD: U3.5 (RC5), U4.4 (FWD)
/IR_DOWN: J5.2, R5.1
/IR_UP: R8.1, SW2.1 (A)
/M1: M1.1 (+), U4.1 (OUT1)
/M2: M1.2 (-), U4.7 (OUT2)
/RA2: SW1.T, U3.11 (RA2)
/RA4: R9.2, RV1.1, RV1.2, RV2.3, U3.3 (RA4)
/RA5: R9.1, R10.2, RV2.1, RV2.2, RV3.3, U3.2 (RA5)
/REV: U3.6 (RC4), U4.5 (REV)
/SCL: J4.4, J7.2, U3.10 (RC0)
/SDA: J4.3, J7.3, U3.9 (RC1)
/Sensor0: J2.3, J9.3, R6.1, SW3.1 (A)
/Sensor1: R13.1, SW3.3 (C), U6.4
GND: C2.2, C3.2, C4.1, C5.2, C7.2, J1.A12 (GND), J1.B12 (GND), J1.S1 (SHIELD), J2.1, J3.3, J4.2, J5.1, J6.2, J8.3, J9.1, JP3.1 (A), R1.2, R2.2, R10.1, R13.2, RV3.1, RV3.2, SW1.C, U1.2, U2.2, U3.14 (VSS), U4.8 (GND), U6.2
unnamed: C3.1, J3.1, R7.1, U3.4 (~MCLR/RA3)
unnamed: C4.2, J3.2, JP2.1 (A), R7.2, U3.1 (VDD)
unnamed: C5.1, JP1.2 (C), U4.2 (VM), U4.3 (VDD), U4.6 (VREF)
unnamed: D1.1 (K), SW3.4 (A)
unnamed: D1.2 (A), D2.2 (A), R15.2
unnamed: D2.1 (K), SW3.6 (C)
unnamed: D3.1 (K), SW1.2
unnamed: D4.1 (K), J6.3
unnamed: J1.A5 (CC1), R2.1
unnamed: J1.B5 (CC2), R1.1
unnamed: J2.2, SW2.3 (C)
unnamed: J3.4, SW3.5 (B), U3.13 (RA0/ICSPDAT)
unnamed: J5.3, U2.4
unnamed: J6.1, JP1.3 (B)
unnamed: J7.1, JP3.2 (C)
unnamed: R4.1, SW1.1
unnamed: R5.2, U2.1
unnamed: R6.2, RV1.3
unnamed: R8.2, U1.1
unnamed: R12.2, U6.1
unnamed: SW3.2 (B), U3.8 (RC2)

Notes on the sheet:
Green
detect feeder hole
1st floor
RA4 RA5 ON - -> White (0-200Ω) OFF ON -> Clear (7k-16k) OFF OFF -> BLACK (18k-39k) ON=0V(GND) OFF=Open-Drain or INPUT @5V, R(LED)=510Ω
3pin=dummy
BD6211 / BD6231
2nd floor
ladder sensor
Red
N.M.
CW/CCW/PUSH Switch
Feeder Hole Sensor
Magnetic Sensor AS5600
hole sensor
Rev.02 * Add CW/CCW Switch * Add Upper IR-LED * Add Magnetic Sensor * Add Sensor Sensitivity Selector (RA4, RA5) * Delete PD IC CH221 * Add Diode OR (D3 and D4)
Sensor Sensitivity Selector
3rd floor

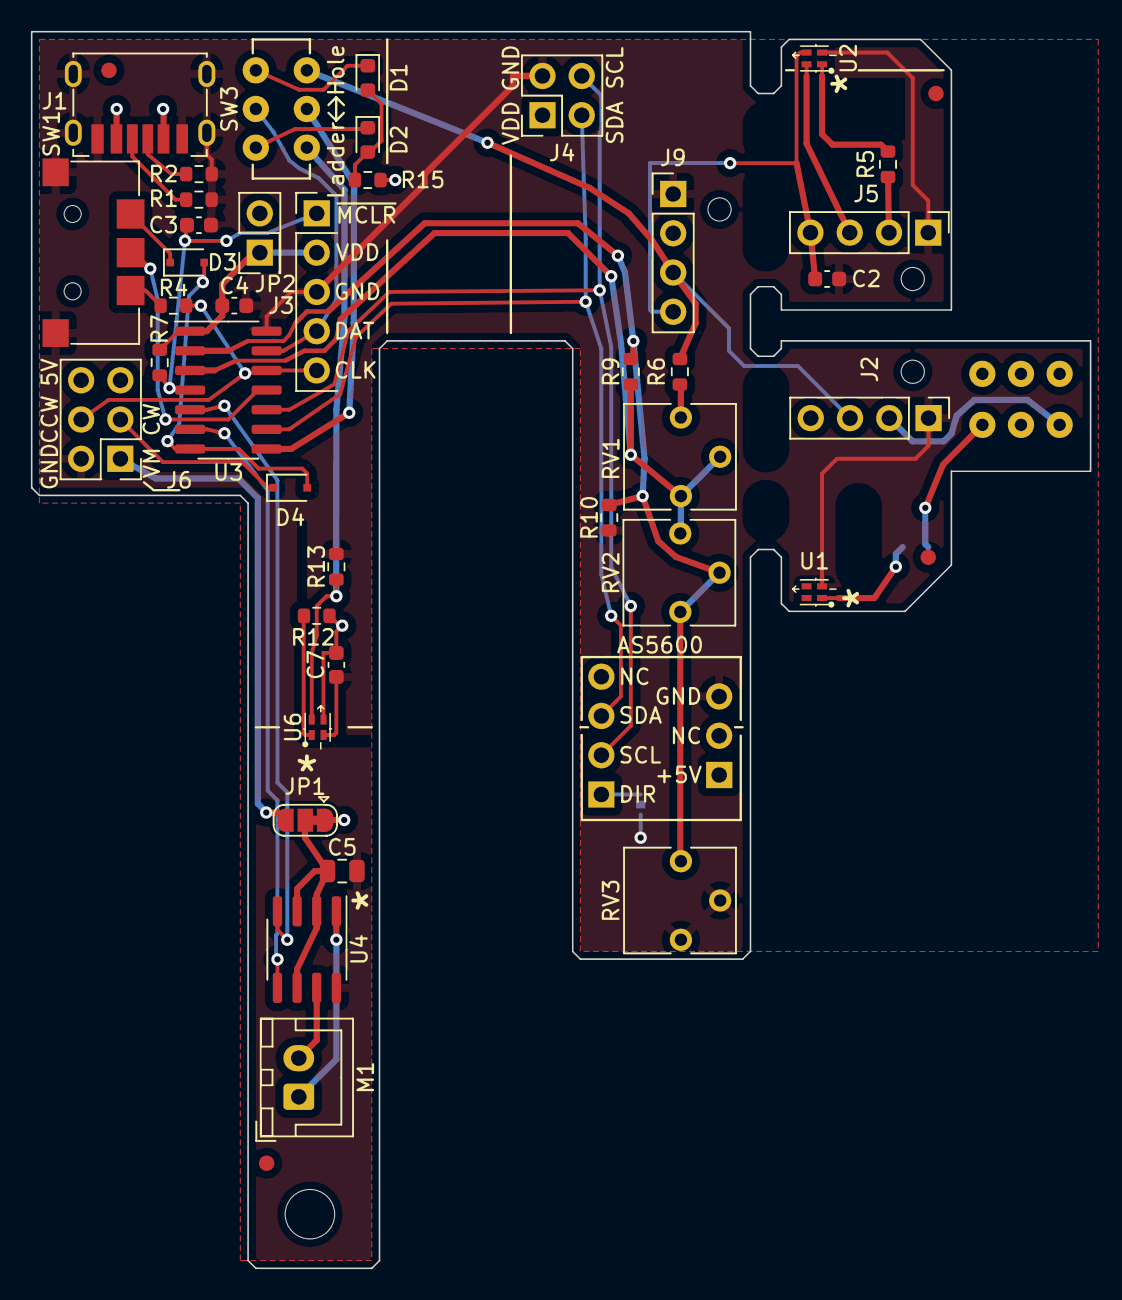
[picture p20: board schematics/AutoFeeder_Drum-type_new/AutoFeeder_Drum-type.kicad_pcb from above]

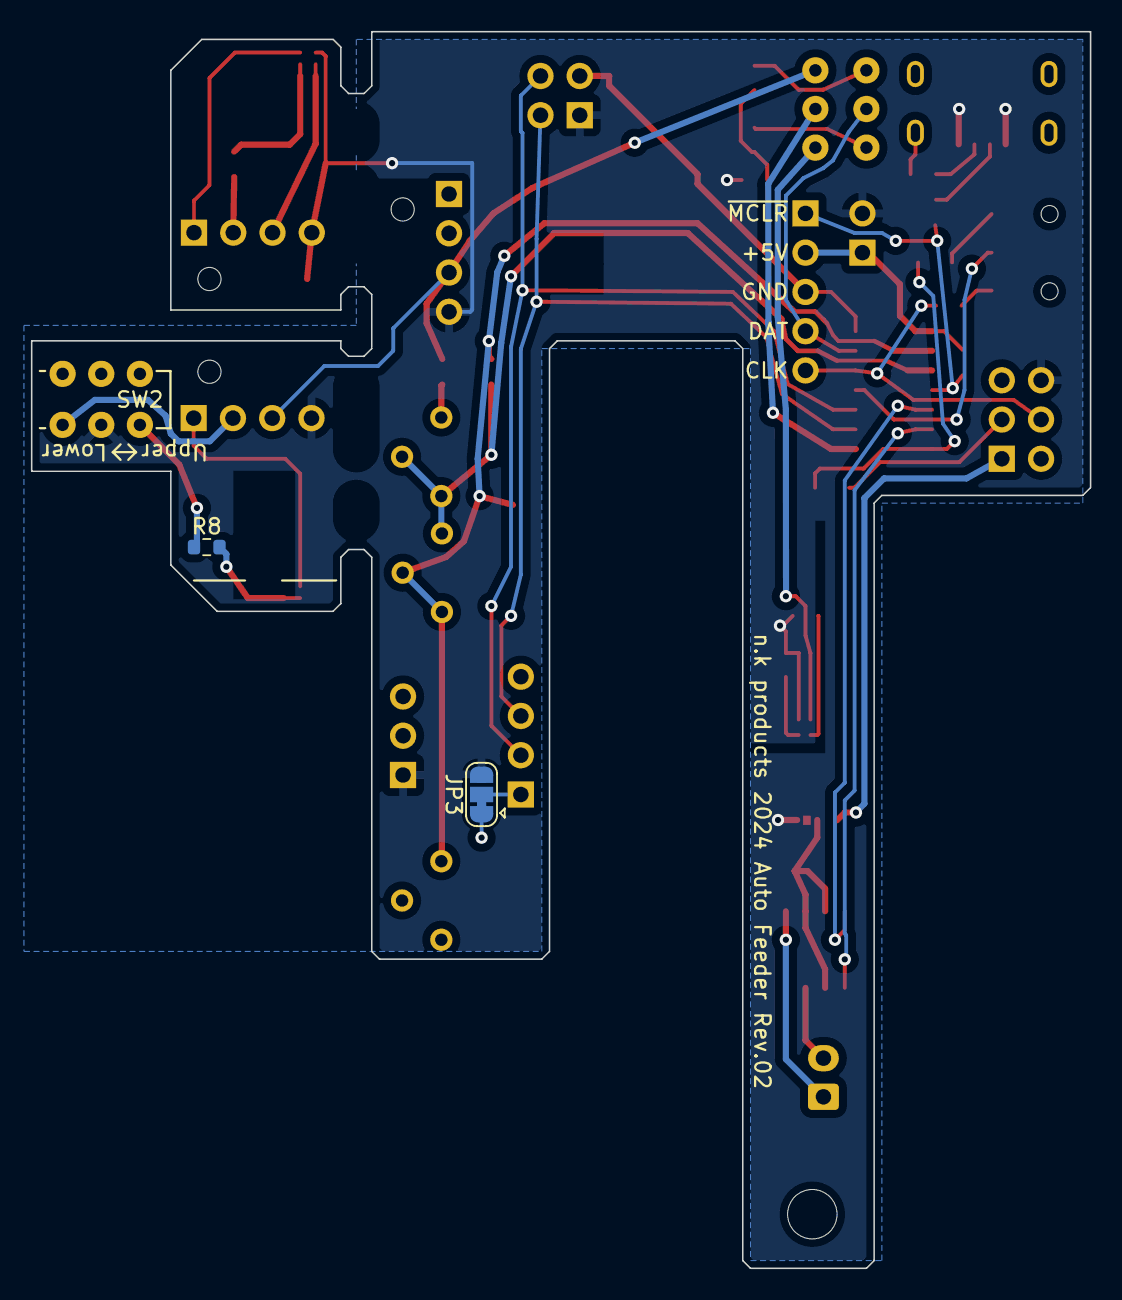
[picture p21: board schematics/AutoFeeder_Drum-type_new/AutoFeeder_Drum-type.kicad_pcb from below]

Board: 2 copper layers, 68.5 x 80.0 mm, 45 parts (3 on the bottom side), 38 nets.

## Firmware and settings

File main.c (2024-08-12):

/**
  Generated Main Source File

  Company:
    Microchip Technology Inc.

  File Name:
    main.c

  Summary:
    This is the main file generated using PIC10 / PIC12 / PIC16 / PIC18 MCUs

  Description:
    This header file provides implementations for driver APIs for all modules selected in the GUI.
    Generation Information :
        Product Revision  :  PIC10 / PIC12 / PIC16 / PIC18 MCUs - 1.81.8
        Device            :  PIC16F1705
        Driver Version    :  2.00
*/

/*
    (c) 2018 Microchip Technology Inc. and its subsidiaries. 
    
    Subject to your compliance with these terms, you may use Microchip software and any 
    derivatives exclusively with Microchip products. It is your responsibility to comply with third party 
    license terms applicable to your use of third party software (including open source software) that 
    may accompany Microchip software.
    
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
    IN NO EVENT WILL MICROCHIP BE LIABLE FOR ANY INDIRECT, SPECIAL, PUNITIVE, 
    INCIDENTAL OR CONSEQUENTIAL LOSS, DAMAGE, COST OR EXPENSE OF ANY KIND 
    WHATSOEVER RELATED TO THE SOFTWARE, HOWEVER CAUSED, EVEN IF MICROCHIP 
    HAS BEEN ADVISED OF THE POSSIBILITY OR THE DAMAGES ARE FORESEEABLE. TO 
    THE FULLEST EXTENT ALLOWED BY LAW, MICROCHIP'S TOTAL LIABILITY ON ALL 
    CLAIMS IN ANY WAY RELATED TO THIS SOFTWARE WILL NOT EXCEED THE AMOUNT 
    OF FEES, IF ANY, THAT YOU HAVE PAID DIRECTLY TO MICROCHIP FOR THIS 
    SOFTWARE.
*/

#include "mcc_generated_files/mcc.h"

#include <stdio.h>
#include <string.h>
#include "mcc_generated_files/examples/i2c_master_example.h"

//Select sensor CNZ1023 or NJL5901AR-1
#define CNZ1023
//#define NJL5901

/******* FLASH *******/
#define FLASH_ROWSIZE   32      //size of a row
#define HEFLASH_START   0x1F80  //first address in HE Flash memory
#define HEFLASH_END     0x1FFF  //last address in HE Flash memory

void _unlock (void){
    asm("BANKSEL PMCON2");
    asm("MOVLW  0x55");
    asm("MOVWF	PMCON2 & 0x7F");
    asm("MOVLW	0xAA");
    asm("MOVWF	PMCON2 & 0x7F");
    asm("BSF    PMCON1 & 0x7F, 1");
    asm("NOP");
    asm("NOP");
} // unlock
unsigned FLASH_readConfig (unsigned address){
    // 1. load the address pointers
    PMADR = address;
    PMCON1bits.CFGS = 1;    //select the configuration Flash address space
    PMCON1bits.RD = 1;  //next operation will be a read
    NOP();
    NOP();
    // 2. return value read
    return PMDAT; 
} // FLASH_config
unsigned FLASH_read (unsigned address) {
    // 1. load the address pointers
    PMADR = address;
    PMCON1bits.CFGS = 0;    //select the Flash address space
    PMCON1bits.RD = 1;      //next operation will be a read
    NOP();
    NOP();
    // 2. return value read
    return PMDAT; 
} // FLASH_read
void FLASH_readBlock (unsigned *buffer, unsigned address, char count) {
    while (count > 0)
    {
        *buffer++ = FLASH_read (address++);
        count--; 
    }
} // FLASH_readBLock
void FLASH_write (unsigned address, unsigned data, char latch) {
    // 1. disable interrupts (remember setting)
    char temp = INTCONbits.GIE;
    INTCONbits.GIE = 0;
    // 2. load the address pointers 
    PMADR = address;
    PMDAT = data;
    PMCON1bits.LWLO = latch;    //1 = latch, 0 = write row
    PMCON1bits.CFGS = 0;    //select the Flash address space
    PMCON1bits.FREE = 0;    //next operation will be a write
    PMCON1bits.WREN = 1;    //enable Flash memory write/erase
    // 3. perform unlock sequence
    _unlock();
    // 4. restore interrupts 
    if (temp)
       INTCONbits.GIE = 1;
}//FLASH_write
void FLASH_erase (unsigned address){
    // 1. disable interrupts (remember setting)
    char temp = INTCONbits.GIE;
    INTCONbits.GIE = 0;
    // 2. load the address pointers 
    PMADR = address;
    PMCON1bits.CFGS = 0;    // select the Flash address space
    PMCON1bits.FREE = 1;    // next operation will be an erase
    PMCON1bits.WREN = 1;    // enable Flash memory write/erase
    // 3. perform unlock sequence and erase 
    _unlock();
    // 4. disable writes and restore interrupts
    PMCON1bits.WREN = 0; // disable Flash memory write/erase 
    if (temp)
       INTCONbits.GIE = 1;
}//FLASH_erase
#define HEFLASH_MAXROWS (HEFLASH_END-HEFLASH_START+1)/FLASH_ROWSIZE
char HEFLASH_writeBlock14 (char radd, unsigned* data, char count) {
    // 1. obtain absolute address in HE FLASH row 
    unsigned add = radd * FLASH_ROWSIZE + HEFLASH_START;
    // 2. check input parameters
    if ((count > FLASH_ROWSIZE)||(radd >= HEFLASH_MAXROWS))
          return (char)-1;//return parameter error
    // 3. erase the entire row 
    FLASH_erase (add);
    // 4. fill the latches with data 
    while (count > 1)
    {
        //load data in latches without writing 
        FLASH_write (add++, *data++, 1); 
        count--;
    } 
    // no delay here!!!
    // 5. last byte of data -> write 
    FLASH_write (add, *data, 0); 
    // NOTE: 2ms typ. delay here!!!
    __delay_ms(2);
    // 6. return success
    return PMCON1bits.WRERR; //0 success, 1 = write error
} //HEFLASH_writeBlock14
char HEFLASH_readBlock14 (unsigned *buffer, char radd, char count) {
    // 1. obtain absolute address in HE FLASH row 
    unsigned add = radd * FLASH_ROWSIZE + HEFLASH_START;
    // 2. check input parameters
    if ((count > FLASH_ROWSIZE)||(radd >= HEFLASH_MAXROWS))
        return (char)-1;
    // 3. read content 
    while (count > 0)
    {
        *buffer++ = FLASH_read (add++);
        count--; 
    }
    // 4. success
    return (char)0;
} //HEFLASH_readBlock
char HEFLASH_readByte (char radd, char offset) {
    // 1. add offset into HE Flash memory
    unsigned add = radd * FLASH_ROWSIZE + HEFLASH_START + offset; 
    // 2. read content
    return (char) FLASH_read (add);
} //HEFLASH_read

/******** I2C ********/
/*
 *  Use MSSP I2C by MCC
 */

/******** I2C LCD ********/
#define LCD_ADDR 0x3E
bool LCD = true;
char DisplayData[8]="12345678";

bool is_I2C_Connected(uint8_t slave_address){
    bool exist_i2c = false;  // true: exist i2c, false: No i2c
    __delay_ms(10);
    if ( (RC0_GetValue() | RC1_GetValue()) != 0){ // if no pull-up
        if( I2C_Open(slave_address) == I2C_NOERR){ 
            exist_i2c = true;
        } else {
            if( I2C_Open(slave_address) == I2C_FAIL ){
                exist_i2c = false;
            } else {
                if( I2C_Open(slave_address) == I2C_BUSY ){
                    exist_i2c = false;
                }
            }
        }
    }
    return exist_i2c;
}
void writeLCDCommand(char t_command){
    I2C_Write1ByteRegister(LCD_ADDR, 0x00, t_command );
    __delay_us(30);     //Instruction Execution Time 14.3-26.3us
}
void LCD_Init(){
    __delay_ms(400);
    writeLCDCommand(0x38);
    writeLCDCommand(0x39);
    writeLCDCommand(0x14);
    writeLCDCommand(0x76);// contast LSB setting ; 0b0111 xxxx
    writeLCDCommand(0x50);// 5V=0b0101 00xx, 3V=0b0101 01xx,  xx=contrast MSB
    writeLCDCommand(0x6C);
    __delay_ms(250);
    writeLCDCommand(0x38);
    writeLCDCommand(0x0C);
    writeLCDCommand(0x01);
    __delay_us(1100);        //Instruction Execution Time 0.59-1.08ms (550:NG, 600:GOOD)
}
void LCD_xy(uint8_t x, uint8_t y){
    writeLCDCommand(0x80 + 0x40 * y + x);
}
void LCD_str2(const char *c) {
    unsigned char wk;
    for (int i=0;i<8;i++){
        wk = c[i];
        if  (wk == 0x00) break;
        I2C_Write1ByteRegister(LCD_ADDR, 0x40, wk );
    }
    __delay_us(30);
}
void LCD_clear(){
    writeLCDCommand(0x01);
    __delay_us(1100);        //Instruction Execution Time 0.59-1.08ms (550:NG, 600:GOOD)
}
void writeLCDData(char t_data){
    I2C_Write1ByteRegister(LCD_ADDR, 0x40, t_data );
    __delay_us(30);     //Instruction Execution Time 14.3-26.3us
}
void LCD_SetCG(const char *c){
    for (int i=0;i<40;i++){
        writeLCDCommand(0x48+(char)i);
        writeLCDData(c[i]);
    }
}

/******** I2C AS5600 ********/
#define AS5600_ADDR 0x36
bool AS5600 = true;//false;
uint8_t ReadBuffer[4];
#define STATUS_MD 0b00100000
#define STATUS_ML 0b00010000
#define STATUS_MH 0b00001000

int readMagData(void){
    int rb16;
    I2C_ReadDataBlock(AS5600_ADDR, 0x0c, ReadBuffer, 2);
    ReadBuffer[2] = ReadBuffer[0] & 0x0f;
    rb16 = ReadBuffer[2];
    ReadBuffer[3] = ReadBuffer[1];
    rb16 = (rb16 << 8) | ReadBuffer[3];
    return rb16;
}
/******** Motor Control ********/
// Motor Direction
#define FWD 1
#define REV 0

void motor_on(int Direction, uint16_t PWM){
    /*
     * PWM range 0..100 (0%..100%) (PWMDC 0..319)
     */
    PWM = PWM * 319 / 100;
    if (Direction ==1){
        PWM4CONbits.PWM4EN = 0; // REV pin = Disable
        RC4_SetLow(); // REV pin = Low
        PWM3_LoadDutyValue(PWM);
        PWM3CONbits.PWM3EN = 1; // FWD pin = Enable
    }
    if (Direction ==0){
        PWM3CONbits.PWM3EN = 0; // FWD pin = Disable
        RC5_SetLow(); // FWD pin = Low
        PWM4_LoadDutyValue(PWM);
        PWM4CONbits.PWM4EN = 1; // REV pin = Enable
    }
}
void motor_off(void){
    PWM3CONbits.PWM3EN = 0; // FWD pin = Disable
    RC5_SetLow(); // FWD pin = Low
    PWM4CONbits.PWM4EN = 0; // REV pin = Disable
    RC4_SetLow();    
}
void motor_brake(void){
    PWM3CONbits.PWM3EN = 0; // FWD pin = Disable
    RC5_SetHigh();
    PWM4CONbits.PWM4EN = 0; // REV pin = Disable
    RC4_SetHigh();    
}
/******** Read Switches ********/
bool isPushed_CCW_SW(void){
    if ( IO_RA1_GetValue() == 0 ){
        return true;
        }
    else {
        return false;
    }    
}
bool isPushed_CW_SW(void){
    if ( IO_RC3_GetValue() == 0 ){
        return true;
        }
    else {
        return false;
    }    
}

bool isPushed_Push_SW(void){
    if ( IO_RA2_GetValue() == 0 ){
        return true;
        }
    else {
        return false;
    }    
}
int pressed_and_held = 0;
bool isPushed_Push_SW_long(void){
    if ( isPushed_Push_SW() ){
        __delay_ms(100);
        pressed_and_held++;
        if ( ( pressed_and_held ) > 20) { // pressed and held 2 second
            pressed_and_held = 0;
            return true;
        }
        return false;
    }
    pressed_and_held = 0;
    return false;
}
/******** Select Sensor sensitivity  ********/
#define ColorWhite 0
#define ColorClear 1
#define ColorBlack 2
const char TapeColorData[4][8] = {"White","Clear","Black","     "};
void setTapeColor(int TapeColor){
    /*
     * Feeder Color 0:White, 1:Clear, 2:Black
     */
    switch (TapeColor){
        case ColorClear: // Clear Color
            IO_RA4_SetHigh();
            IO_RA5_SetLow();
            break;
        case ColorBlack: // Black Color
            IO_RA4_SetHigh();
            IO_RA5_SetHigh();
            break;
        default: // White Color
            IO_RA4_SetLow();
            IO_RA5_SetLow();
    }
}
/******** Detect Tape hole  ********/
bool isExist_Hole(){
    int i;
    int tapeExist = 0;
    // Move to forward for 1 second
    motor_on(FWD, 100);
    for(i=0;i<100;i++){
        __delay_ms(10);
        if (RA0_GetValue() == 1){
            tapeExist++;
            break;  // Exit if not detect hole
        }
    }
    // Move to backward for 1 second
    motor_on(REV, 100);
    for(i=0;i<100;i++){
        __delay_ms(10);
        if (RA0_GetValue() == 0){
            tapeExist++;
            break;  // Exit when hole is detected
        }
    }
    if (tapeExist == 2) { return true; } else return false;
}
/******** Rotate direction close to the target  ********/
void RotateToTarget(int TargetAngle){
    int DiffAngle, currentDirection, currentMagData;
    bool farDistance = true;
    currentMagData = readMagData();
    DiffAngle = currentMagData + 4096 - TargetAngle;
    if (DiffAngle > 4095) DiffAngle -= 4096;
    if( 0 > ( DiffAngle - 2048 ) ) 
        currentDirection = REV;//FWD; 
    else 
        currentDirection = FWD;//REV;
    motor_on(currentDirection, 80);
    do {
        __delay_ms(10);
        currentMagData = readMagData();
        if (LCD){
            sprintf(DisplayData, "%04d", currentMagData); 
            LCD_xy(0,0); LCD_str2( DisplayData );
        }
        if ( farDistance && (((TargetAngle +30) > currentMagData) && ((TargetAngle -30) < currentMagData)) ) {
            motor_on(currentDirection, 45);
            farDistance = false;
        }
    } while ( ((TargetAngle +4) < currentMagData) || ((TargetAngle -4) > currentMagData) );
    motor_brake();
    //if (LCD) LCD_clear();
}
/******** Move one frame using the results of the optical sensor  ********/
void detectHoleByOptical(){
    motor_on(FWD, 100);
    __delay_ms(50);
    while( RA0_GetValue() == 1 ){   // Loop on tape section
        if( isPushed_CCW_SW() ) break;
    }
    motor_on(FWD, 100);
    __delay_ms(10);
    while( RA0_GetValue() == 0 ){   // Loop on hole section
        if( isPushed_CCW_SW() ) break;
    }
    motor_brake();
}

/*
                         Main application
 */


void main(void)
{
    // initialize the device
    SYSTEM_Initialize();

    // When using interrupts, you need to set the Global and Peripheral Interrupt Enable bits
    // Use the following macros to:

    // Enable the Global Interrupts
    //INTERRUPT_GlobalInterruptEnable();

    // Enable the Peripheral Interrupts
    //INTERRUPT_PeripheralInterruptEnable();

    // Disable the Global Interrupts
    //INTERRUPT_GlobalInterruptDisable();

    // Disable the Peripheral Interrupts
    //INTERRUPT_PeripheralInterruptDisable();

    /*
     * High-Endurance Flash(HEF)
     * 
     * HEF_buffer14[0] : AS5600 Magnetic data 12bit
     * HEF_buffer14[1] : stored Tape-Color data
     * HEF_buffer14[2..24] : stored tape hole position data
     */
    unsigned HEF_buffer14[FLASH_ROWSIZE];
    unsigned r;
    int i;
    bool CW_is_being_pressed = false;
    int CW_counter, CW_Release_counter;

    motor_off();
    LCD = is_I2C_Connected(LCD_ADDR);
    if (LCD) {
        LCD_Init();
        LCD_clear();
    }
    AS5600 = is_I2C_Connected(AS5600_ADDR);
    //for test
    //AS5600 = false;
    
    // Resore all data from High-Endurance Flash(HEF)
    r = HEFLASH_readBlock14 (HEF_buffer14, 0, FLASH_ROWSIZE);

    /*
     *  Restore Tape Color
     */
    /*if ( (HEF_buffer14[1] != ColorWhite ) 
            && (HEF_buffer14[1] != ColorClear ) 
            && (HEF_buffer14[1] != ColorBlack) )
        HEF_buffer14[1]=0;    // set default color white when no-data
    setTapeColor((int)HEF_buffer14[1]);
    if (LCD) {
        sprintf(DisplayData, "%s", TapeColorData[ HEF_buffer14[1] ] );
        LCD_xy(0,0); LCD_str2( DisplayData );
        __delay_ms(1000);
    }*/

    /*
     *  Detect current Tape Color
     */
#ifdef NJL5901
    for(i=0;i<4;i++){
        setTapeColor(i);    // 0:White, 1:Clear, 2:Black
        if ( isExist_Hole() ) break;
    }
    if (i < 3) {
        if (LCD) sprintf(DisplayData, "%s", TapeColorData[i]);
    } else {
        i = 0;
        if (LCD) sprintf(DisplayData, "%s", "No tape");
    }
#endif
#ifdef CNZ1023
    i = ColorBlack;
    setTapeColor(i);    // 0:White, 1:Clear, 2:Black
    if (LCD) sprintf(DisplayData, "%s", "BK or WH");
#endif
    HEF_buffer14[1] = (unsigned)i;
    if (LCD) { LCD_xy(0,0); LCD_str2( DisplayData ); }
    __delay_ms(1000);
    if (LCD) { LCD_clear(); }

    if (false) { //AS5600) {
        /*
         *  Restore default drum Position
         */
        if (LCD){
            sprintf(DisplayData, "%04d", HEF_buffer14[0]);
            LCD_xy(0,1); LCD_str2( DisplayData );
            sprintf(DisplayData, "%02x", SSP1ADD);  //Display I2C Speed for test
            LCD_xy(6,1); LCD_str2( DisplayData );
            __delay_ms(1000);
        }
        //  Rotate direction close to the target drum position
        RotateToTarget((int) HEF_buffer14[0] );
        
        // Trace the position of memorized values
        __delay_ms(1000);
        for(i=1;i<=22;i++){ // i=1 : Ignore the first data
            if (LCD){
                sprintf(DisplayData, "%04d  %02d", HEF_buffer14[2+i], i);
                LCD_xy(0,1); LCD_str2( DisplayData );
            }
            RotateToTarget((int) HEF_buffer14[2+i] );
            __delay_ms(500);
        }
        if (LCD) {
            LCD_clear();
            LCD_xy(0,0); LCD_str2( "Rewind!" );
        }
        motor_on(REV, 100);
        __delay_ms(12000);     //move to near by target
        if (LCD) LCD_clear();
        RotateToTarget((int) HEF_buffer14[0] );
    }
    motor_brake();
    if (AS5600) {
        if (LCD) LCD_clear();
    }

    CW_counter = 0;
    CW_Release_counter = 0;
    
    while (1)
    {
        // Add your application code
        
        /*
         *  move forward one frame if CW pushed
         * Pressing CW advances one frame using the results of the optical sensor.
         */
        if ( isPushed_CW_SW() ){
            if ( !CW_is_being_pressed ){
                CW_is_being_pressed = true;
                CW_counter = 0;
                CW_Release_counter = 0;
                while (RC3 == 0) {
                    __delay_ms(1);  // reject fall edge chatter
                    CW_counter++;
                    if (CW_counter > 5){
                        detectHoleByOptical();
                        break;
                    }
                }
            }
        } else {
            while ((RC3 == 1) && CW_is_being_pressed) {
                __delay_ms(1);  // reject rise edge chatter
                CW_Release_counter++;
                if (CW_Release_counter > 5){
                    CW_is_being_pressed = false;
                    break;
                }
            }
        }

        /*
         *  Move backward while CCW is pressed
         */
        if ( isPushed_CCW_SW() ){
                motor_on(REV, 100);
        } else {
            motor_brake();
        }

        /*
         *  Memorize rotation angle and tape color to EEPROM when SW was pushed
         */
        if ( isPushed_Push_SW_long() ){
            if (AS5600) {
                //Save Mag Position
                HEF_buffer14[0] = (unsigned) readMagData();
            }

            // Memorizes 21 hole positions
            if (AS5600) {
                for(i=0;i<=22;i++){
                    detectHoleByOptical();
                    HEF_buffer14[2+i] = (unsigned) readMagData() ;
                    sprintf(DisplayData, "%04d", HEF_buffer14[2+i]); 
                    LCD_xy(0,0); LCD_str2( DisplayData );  
                    __delay_ms(200);
                }
                // Store all data to HEF
                r = HEFLASH_writeBlock14(0, HEF_buffer14, FLASH_ROWSIZE);
                if (LCD) {
                    LCD_clear();
                    LCD_xy(0,0); LCD_str2( "Rewind!" );
                }
                motor_on(REV, 100);
                __delay_ms(12000);   //move to near by target
                if (LCD) LCD_clear();
                motor_brake();
                RotateToTarget((int) HEF_buffer14[0] );
            }
        }
        
        if (LCD && AS5600){
            sprintf(DisplayData, "%04d", readMagData()); 
            LCD_xy(0,0); LCD_str2( DisplayData );
            I2C_ReadDataBlock(AS5600_ADDR, 0x0b, ReadBuffer, 1);
            if ( (ReadBuffer[0] & STATUS_MD) != 0 ){
                sprintf(DisplayData, "MAG    ");
            } else {
                sprintf(DisplayData, "        ");
            }
            LCD_xy(0,1); LCD_str2( DisplayData );
            if ( (ReadBuffer[0] & STATUS_ML) != 0){
                sprintf(DisplayData, "L");
            } else {
                if ( (ReadBuffer[0] & STATUS_MH) != 0){
                    sprintf(DisplayData, "H");
                } else {
                    sprintf(DisplayData, " ");
                }
            }
            LCD_xy(7,1); LCD_str2( DisplayData );
        }
    }
}
/**
 End of File
*/

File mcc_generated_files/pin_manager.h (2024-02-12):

/**
  @Generated Pin Manager Header File

  @Company:
    Microchip Technology Inc.

  @File Name:
    pin_manager.h

  @Summary:
    This is the Pin Manager file generated using PIC10 / PIC12 / PIC16 / PIC18 MCUs

  @Description
    This header file provides APIs for driver for .
    Generation Information :
        Product Revision  :  PIC10 / PIC12 / PIC16 / PIC18 MCUs - 1.81.8
        Device            :  PIC16F1705
        Driver Version    :  2.11
    The generated drivers are tested against the following:
        Compiler          :  XC8 2.36 and above
        MPLAB 	          :  MPLAB X 6.00	
*/

/*
    (c) 2018 Microchip Technology Inc. and its subsidiaries. 
    
    Subject to your compliance with these terms, you may use Microchip software and any 
    derivatives exclusively with Microchip products. It is your responsibility to comply with third party 
    license terms applicable to your use of third party software (including open source software) that 
    may accompany Microchip software.
    
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
    IN NO EVENT WILL MICROCHIP BE LIABLE FOR ANY INDIRECT, SPECIAL, PUNITIVE, 
    INCIDENTAL OR CONSEQUENTIAL LOSS, DAMAGE, COST OR EXPENSE OF ANY KIND 
    WHATSOEVER RELATED TO THE SOFTWARE, HOWEVER CAUSED, EVEN IF MICROCHIP 
    HAS BEEN ADVISED OF THE POSSIBILITY OR THE DAMAGES ARE FORESEEABLE. TO 
    THE FULLEST EXTENT ALLOWED BY LAW, MICROCHIP'S TOTAL LIABILITY ON ALL 
    CLAIMS IN ANY WAY RELATED TO THIS SOFTWARE WILL NOT EXCEED THE AMOUNT 
    OF FEES, IF ANY, THAT YOU HAVE PAID DIRECTLY TO MICROCHIP FOR THIS 
    SOFTWARE.
*/

#ifndef PIN_MANAGER_H
#define PIN_MANAGER_H

/**
  Section: Included Files
*/

#include <xc.h>

#define INPUT   1
#define OUTPUT  0

#define HIGH    1
#define LOW     0

#define ANALOG      1
#define DIGITAL     0

#define PULL_UP_ENABLED      1
#define PULL_UP_DISABLED     0

// get/set RA0 procedures
#define RA0_SetHigh()            do { LATAbits.LATA0 = 1; } while(0)
#define RA0_SetLow()             do { LATAbits.LATA0 = 0; } while(0)
#define RA0_Toggle()             do { LATAbits.LATA0 = ~LATAbits.LATA0; } while(0)
#define RA0_GetValue()              PORTAbits.RA0
#define RA0_SetDigitalInput()    do { TRISAbits.TRISA0 = 1; } while(0)
#define RA0_SetDigitalOutput()   do { TRISAbits.TRISA0 = 0; } while(0)
#define RA0_SetPullup()             do { WPUAbits.WPUA0 = 1; } while(0)
#define RA0_ResetPullup()           do { WPUAbits.WPUA0 = 0; } while(0)
#define RA0_SetAnalogMode()         do { ANSELAbits.ANSA0 = 1; } while(0)
#define RA0_SetDigitalMode()        do { ANSELAbits.ANSA0 = 0; } while(0)

// get/set IO_RA1 aliases
#define IO_RA1_TRIS                 TRISAbits.TRISA1
#define IO_RA1_LAT                  LATAbits.LATA1
#define IO_RA1_PORT                 PORTAbits.RA1
#define IO_RA1_WPU                  WPUAbits.WPUA1
#define IO_RA1_OD                   ODCONAbits.ODA1
#define IO_RA1_ANS                  ANSELAbits.ANSA1
#define IO_RA1_SetHigh()            do { LATAbits.LATA1 = 1; } while(0)
#define IO_RA1_SetLow()             do { LATAbits.LATA1 = 0; } while(0)
#define IO_RA1_Toggle()             do { LATAbits.LATA1 = ~LATAbits.LATA1; } while(0)
#define IO_RA1_GetValue()           PORTAbits.RA1
#define IO_RA1_SetDigitalInput()    do { TRISAbits.TRISA1 = 1; } while(0)
#define IO_RA1_SetDigitalOutput()   do { TRISAbits.TRISA1 = 0; } while(0)
#define IO_RA1_SetPullup()          do { WPUAbits.WPUA1 = 1; } while(0)
#define IO_RA1_ResetPullup()        do { WPUAbits.WPUA1 = 0; } while(0)
#define IO_RA1_SetPushPull()        do { ODCONAbits.ODA1 = 0; } while(0)
#define IO_RA1_SetOpenDrain()       do { ODCONAbits.ODA1 = 1; } while(0)
#define IO_RA1_SetAnalogMode()      do { ANSELAbits.ANSA1 = 1; } while(0)
#define IO_RA1_SetDigitalMode()     do { ANSELAbits.ANSA1 = 0; } while(0)

// get/set IO_RA2 aliases
#define IO_RA2_TRIS                 TRISAbits.TRISA2
#define IO_RA2_LAT                  LATAbits.LATA2
#define IO_RA2_PORT                 PORTAbits.RA2
#define IO_RA2_WPU                  WPUAbits.WPUA2
#define IO_RA2_OD                   ODCONAbits.ODA2
#define IO_RA2_ANS                  ANSELAbits.ANSA2
#define IO_RA2_SetHigh()            do { LATAbits.LATA2 = 1; } while(0)
#define IO_RA2_SetLow()             do { LATAbits.LATA2 = 0; } while(0)
#define IO_RA2_Toggle()             do { LATAbits.LATA2 = ~LATAbits.LATA2; } while(0)
#define IO_RA2_GetValue()           PORTAbits.RA2
#define IO_RA2_SetDigitalInput()    do { TRISAbits.TRISA2 = 1; } while(0)
#define IO_RA2_SetDigitalOutput()   do { TRISAbits.TRISA2 = 0; } while(0)
#define IO_RA2_SetPullup()          do { WPUAbits.WPUA2 = 1; } while(0)
#define IO_RA2_ResetPullup()        do { WPUAbits.WPUA2 = 0; } while(0)
#define IO_RA2_SetPushPull()        do { ODCONAbits.ODA2 = 0; } while(0)
#define IO_RA2_SetOpenDrain()       do { ODCONAbits.ODA2 = 1; } while(0)
#define IO_RA2_SetAnalogMode()      do { ANSELAbits.ANSA2 = 1; } while(0)
#define IO_RA2_SetDigitalMode()     do { ANSELAbits.ANSA2 = 0; } while(0)

// get/set IO_RA4 aliases
#define IO_RA4_TRIS                 TRISAbits.TRISA4
#define IO_RA4_LAT                  LATAbits.LATA4
#define IO_RA4_PORT                 PORTAbits.RA4
#define IO_RA4_WPU                  WPUAbits.WPUA4
#define IO_RA4_OD                   ODCONAbits.ODA4
#define IO_RA4_ANS                  ANSELAbits.ANSA4
#define IO_RA4_SetHigh()            do { LATAbits.LATA4 = 1; } while(0)
#define IO_RA4_SetLow()             do { LATAbits.LATA4 = 0; } while(0)
#define IO_RA4_Toggle()             do { LATAbits.LATA4 = ~LATAbits.LATA4; } while(0)
#define IO_RA4_GetValue()           PORTAbits.RA4
#define IO_RA4_SetDigitalInput()    do { TRISAbits.TRISA4 = 1; } while(0)
#define IO_RA4_SetDigitalOutput()   do { TRISAbits.TRISA4 = 0; } while(0)
#define IO_RA4_SetPullup()          do { WPUAbits.WPUA4 = 1; } while(0)
#define IO_RA4_ResetPullup()        do { WPUAbits.WPUA4 = 0; } while(0)
#define IO_RA4_SetPushPull()        do { ODCONAbits.ODA4 = 0; } while(0)
#define IO_RA4_SetOpenDrain()       do { ODCONAbits.ODA4 = 1; } while(0)
#define IO_RA4_SetAnalogMode()      do { ANSELAbits.ANSA4 = 1; } while(0)
#define IO_RA4_SetDigitalMode()     do { ANSELAbits.ANSA4 = 0; } while(0)
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

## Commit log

2023-12-19 Add an image and the schematics.
2023-12-29 Program: Add I2C function; Add LCD; Add Magnetic sensor; Schematics: Add KiCAD files
    [AutoFeeder_Drum-type-B_Cu.gbl, AutoFeeder_Drum-type-B_Mask.gbs, AutoFeeder_Drum-type-B_Paste.gbp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]
2023-12-30 Tried non-volatile memory (High-Endurance FLASH MEMORY). http://ww1.microchip.com/downloads/en/appnotes/00001673a.pdf XC8 has been updated and the manner in which inline assemblers are written has ch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
2023-12-31 Test reading/writing from/to HEF-block
    [AutoFeeder_Drum-type.kicad_pcb]
2024-01-07 Rev.02: Rev01 had a problem with the deep feeder hitting the PCB. Rev02 avoided this problem by overlapping two PCBs for the sensor section.; Three sensitivity options are available for white, transp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
    [AutoFeeder_Drum-type-B_Cu.gbl, AutoFeeder_Drum-type-B_Mask.gbs, AutoFeeder_Drum-type-B_Paste.gbp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]
2024-01-08 Change Schematics; Add Red LED for ladder sensor; Add guide line of feeder tape
    [AutoFeeder_Drum-type-B_Cu.gbl, AutoFeeder_Drum-type-B_Mask.gbs, AutoFeeder_Drum-type-B_Paste.gbp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]
2024-01-08 PCB modification: Slightly lengthened the pins of the USB Type-C connector to improve solderability.
    [AutoFeeder_Drum-type-B_Cu.gbl, AutoFeeder_Drum-type-B_Mask.gbs, AutoFeeder_Drum-type-B_Paste.gbp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]
2024-01-08 Change schematics: Assign CW/CCW pin to connector; Add M3 mounting hole
    [AutoFeeder_Drum-type-B_Cu.gbl, AutoFeeder_Drum-type-B_Mask.gbs, AutoFeeder_Drum-type-B_Paste.gbp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]
2024-01-08 Schematics: Add +5V to J6; Fine-tuning of patterns
    [AutoFeeder_Drum-type-B_Cu.gbl, AutoFeeder_Drum-type-B_Mask.gbs, AutoFeeder_Drum-type-B_Paste.gbp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]
2024-01-09 Schematics: Add Diode OR (D3 and D4) for manual feed and auto feed
    [AutoFeeder_Drum-type-B_Cu.gbl, AutoFeeder_Drum-type-B_Mask.gbs, AutoFeeder_Drum-type-B_Paste.gbp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]
2024-01-16 Change the position of M3 mounting hole / Add silk printing of magnetic sensor / Add Diode OR (D3,D4) to allow advancing one component either by manual switch or automatic control / Slightly modified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
    [AutoFeeder_Drum-type-B_Cu.gbl, AutoFeeder_Drum-type-B_Mask.gbs, AutoFeeder_Drum-type-B_Paste.gbp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]
2024-02-12 Support Rev.02 PCB.
    [AutoFeeder_Drum-type.kicad_pcb]
2024-02-18 When the power is turned on, rotate in the direction closest to the distance of the stored magnetic sensor value.
2024-02-23 Made code easier to read; Subroutines, comments, etc.; Add Open-PnP files
    [AutoFeeder_Drum-type.ods]
2024-03-03 Add a circuit to switch the sensitivity of the photo sensor, a magnetic sensor named AS5600 to get the angle of the drum, and the LCD.
2024-04-27 An IOC interrupt was used to detect the falling edge of the CW switch; two timers Timer4/Timer6 were used to eliminate the chatter that occurs on the falling and rising edges of the CW switch. These 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
    [AutoFeeder_Drum-type.kicad_sch]
2024-05-04 Changed to a method that does not use interrupts to remove chatter.
2024-07-28 AutoFeeder_Drum-type_new --> AutoFeeder_Drum-type_2 : Change a board that was placed horizontally to vertically.
    [AutoFeeder_Drum-type-B_Cu.gbl, AutoFeeder_Drum-type-B_Mask.gbs, AutoFeeder_Drum-type-B_Paste.gbp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]
2024-08-12 Two types of sensors CNZ1023 and NJL5901 are supported. When the center button is pressed and held for 2 seconds, the hole position is memorized for one revolution, then returns to the original posit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
    [AutoFeeder_Drum-type.kicad_pcb, AutoFeeder_Drum-type.kicad_sch]
2024-08-20 Auto Feeder 2 rev.1 ; The board is placed vertically to save space. Transmissive photo interrupter CNZ1023 can also be used.
    [AutoFeeder_Drum-type-B_Cu.gbl, AutoFeeder_Drum-type-B_Mask.gbs, AutoFeeder_Drum-type-B_Paste.gbp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]
